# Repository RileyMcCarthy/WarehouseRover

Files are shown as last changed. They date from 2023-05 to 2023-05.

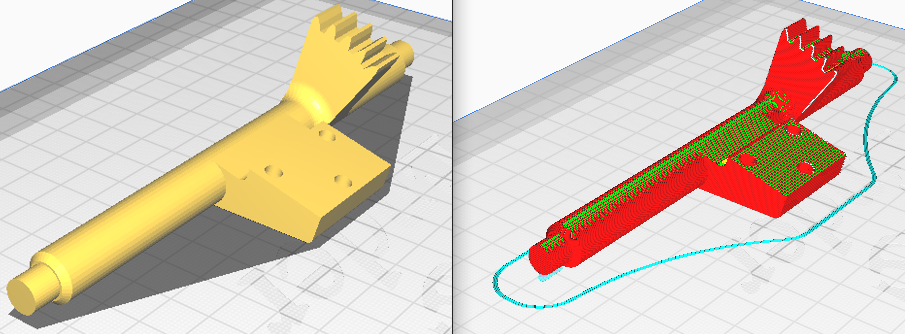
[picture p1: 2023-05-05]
Images/files/ShaftPrint.png

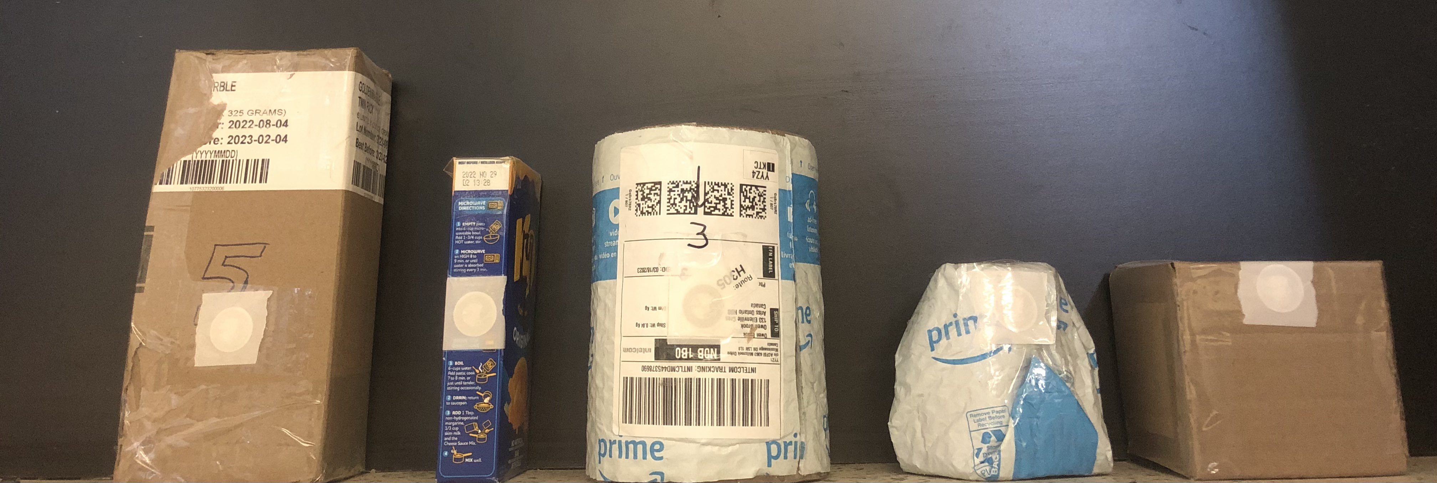
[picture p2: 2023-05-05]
Images/files/packages.jpg

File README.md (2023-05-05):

# Autonomous Sorting Mobile Robot

University of Guelph 4th year project by: Riley McCarthy, Owen Brook, Kaden Penner, Charles Peters, and Nicholas Virdiramo 

## Introduction

With the new Amazon fulfilment center being built in Cambridge, the need for automation
is ever increasing. As the number of outbound packages increase, so will the number of
returns that need to be processed. This is one example of where using automation will allow
processes to become more streamlined and efficient. Our project demonstrates the ability
of these robots in a small scale environment. We designed and developed an autonomous
sorting robot that takes packages from a starting location, identifies it, and then moves it to
the appropriate final location.

This will help the efficiency of large factories as the need for humans to move parts around
the building will be eliminated. With the new Amazon warehouse being 136,000 sqft, small
electric robots moving packages will be more efficient when compared to humans needing to
walk around.

## Objectives

The team aimed to develop an autonomous robot that sorted multiple package variations
between unique locations one at a time. The robot would receive an input from a package
at the starting location and determine the desired final location. Then autonomously would
deliver the package to the correct destination. A block diagram of the robots functions is
shown below.

**Insert block diagrm ref**

The system is completely automated, with the only external input being the placement of
the package in the starting location by a human. This mimicked the use of a conveyor belt
for accurate package delivery to the initial location. Our initial goal was to a system that
could handle three different package shapes with weight variations. This would ensure the
robot was capable of a wide verity of packages shapes and sizes, as well as a range of different
weights. Each package would have it’s own unique destination determined by an RFID sensor
to mimic a scanner being able to identify the incommoding packages and determining their
final locations.

## Mechanical Design

As the goal of the project is to both pickup and move packages, the mechanical design
needed to allow for both a movable main base, the ability to interact with the different
package sizes, and contain all the necessary parts to make the robot autonomous such as a
battery, sensors, and a micro-controller.
Shown below is the initial design of the Autonomous Sorting Mobile Robot.
While the specifics of the different components will be covered later, the motors and
ultrasonic sensors are shown, as well as the wheels, gripper mechanism, and main base of the
robot.

**Figure 2: Robot Isometric View**

The largest part of the robot is the main base. This houses the four
driving motors, two ultrasonic sensors mounts, the control system electronics, and a base for
the grippers to be fastened. Initially the base was designed to be very compact, but this
limited space under for the electronics and motors so the base was increased in size slightly
to accommodate with out overly compromising the compact design This based is designed
an manufactured to provide a strong, square foundation for the robot to operate from. The
strength of the base allowed for the robot to handle larger packages then original considered.
The square base allows for the mecanum wheels to operate as intended and no adjustment
in software needed for straight driving.

**Figure 3: Robot Base with Drive Motors, Sensors and Control System**

The gripper mechanism is driven by two motors. The first is to open and close the grippers,
while the other allows for tilting gripper assembly to lift the package off the ground. The
RFID sensor is mounted to the gripper mechanism at the base of the arms to allow for
the robot to read the package. This allows the control system to determine the correct
destination.

**Figure 4: Gripper System with RFID Sensor**

The grippers are designed to allow for the manipulation of various package sizes to be
interacted with. The initial design is shown in **Figure 4**. The design was tested and found
not to have adequate holding power for the different shapes and sizes. With the fingers of
the arms in an arc shape they only provided one point of contact and resulted in the robot
dropping packages. The arms were also found to be short not allowing enough room for the
fingers to contact he center of the package. These issues were discovered through testing,
and the solution is explained in Section 2.3.

A rack and pinion gripper design was also tested and compared to
look at the load capacity of our designs. This design is secondary and serves as a backup to
our main gripper assembly. This design may be beneficial because it is more compact and
requires less moving parts, resulting in greater grip strength. However, the rack may seize
due to friction between the rack and slide plate when the gripper is under load. For these
reasons, this gripper was not used on the final robot.

**Figure 5: Rack and Pinion Gripper**

## Fabrication

In order to physically build the robot, all the designed components were fabricated using
a 3D printer. This method was chosen as it allows for a wide range of part geometry and
features, with rapid prototyping. The group had direct access to four 3D printers, so the
fabrication of the components was not a problem. Other methods were considered but with
the accessibility and range of builds the 3D printer was chosen
Since we printed all of our parts, material selection was greatly simplified as we could
only print plastics. Furthermore, the forces involved with this robot were low enough where
material strengths did not limit the function of the robot. Plastic is also beneficial as it is
easily manipulated to fit together. Our design contains interference fits (bearings and gears)
that rely on friction and a high normal force to maintain their position. We used heat to
expanded and soften the plastic to fit the components together. Many components were also
filed and sanded after they were printed to remove imperfections from the print, such as
strings, blobs, and support material. This was especially true for parts where a precise fit
was needed or printing orientation effected quality.
Most components were printed using PLA as it is the easiest and most reliable print
material available. PETG, a more dense plastic, was also used for additional strength, for
example, the tilt shaft. The load bearing components were fabricated with 5 layers of material
on the outside surfaces for additional strength. The rest of the parts only required 2-3 layers.
Furthermore, 20-30 percent infill was used on most parts but was varied for based on the
components needs.

**Figure 6: Cura Slicer Print Estimate**

We got material estimates from Ultimaker Cura, the 3D printing slicer. This software allowed the team to understand and control the fabrication of each part.
Adjusting prints based on their geometry, fit, and function allowed for best performance. An
example of the importance of this is the fabrication of the tilt shaft. The shaft needed a
strong and circular geometry. These qualities conflict in the printing orientation, horizontal
for strength and vertical for circular geometry. This is because when it is printed horizontally
it has continuous strings of plastic along its length, increasing strength against bending.
When printed vertically the print is able to precisely outline the circular geometry and avoid
overhanging. Ultimately horizontally was chosen as the strength is more important and the
circular geometry can be adjusted by sanding after. Below shows supports under the step
in the Tilt Shaft.

**Figure 7: Cura Slicer Shaft Print Estimate**

The proposed design from report one (shown in **Figure 8**) was fabricated, assembled, and
tested. The initial testing showed that the gripper fingers were limited in their ability to pick
up the required variety of packages.

**Figure 8: Original Gripper Design**

The final gripper design was an iteration of the first design, improving on all the issues
that caused reliability problems. In the final design (shown in **Figure 9**), the arms and fingers
were redesigned to have longer reach and a pivoting crescent finger for dual point contact.
These worked flawlessly in picking up and holding the package during transportation for
several packages all with different sizes, geometry, and weight.

**Figure 9: Updated Gripper Design**

Additional mechanical testing was done to test the robot’s grip strength and ability to raise
and lower the package. Deflection of the gripper top plate was observed when the gripper
fingers closed. This is due to the torque generated by the gripper motor during package pick
up. The top plate was reinforced and reprinted to prevent failure.

## Motors and Actuators

3.1.1 Four DC Motors with Encoders
As the design places a priority on movement accuracy rather than speed, motors were
selected that contained rotary encoders, allowing for accurate tracking of the rotation of
each wheel. This allowed for a control system algorithm to be created that ensure accurate
movement. Motion planning was also incorporated ensuring adequate traction is always
maintained by limiting the acceleration of the robot’s velocity. The encoders present in these
motors contain 140 ticks per revolution. The motors were been tested to max out at 190 rpm
while running at 12v.
3.1.2 Two DC Motors with Gearboxes
In order to provide movement to the grippers, motors were used to manipulate the grippers.
To ensure the ability to manipulate packages of different sizes and weights, these motors
required sufficient torque which was provided by the gearbox. Tests were conducted to
calculate the amount of torque they were capable of providing when run at 12v. This was
determined to be 0.583 Nm of torque. These motors were controlled with the amount of
current being drawn and were programmed to hold their position when open, or a package
was sufficiently held.
3.1.3 Motor Drivers
These motors will be driven by an L293 motor driver[1]. These drivers allowed for the
motors to be speed-controlled by using pulse wave modulation (PWM). This also allowed for
the direction to be adjusted using the microcontroller.
8
GROUP 3 A.S.M. Robot
3.2 Sensors
3.2.1 Ultrasonic Sensors
To ensure accurate positioning was maintained over time, an ultrasonic sensor was used to
re-home the robot upon its return to the starting/pick-up location. This allowed the robot
to determine its current location, and adjust to ensure location error didn’t accumulate over
time. An HC-SR04 ultrasonic sensor[2] was used as it had been used by the group before,
and are easily available. It had sufficient accuracy to ensure the robot could return to the
desired location between the delivery of each package. The ultrasonic sensor has a large
range of 2cm to 400cm and an accuracy of 2mm which was adequate accuracy and range for
the purpose of our system.
3.2.2 RFID Sensor
In order to determine the final destination for each individual package, a Radio Frequency
Identification Device (RFID) was decided on. While in the future implementation, a more
widely used technology could be used. For testing, the RFID system was easy to implement,
and the component required belong to members of the group. The specific sensor used was
a MFRC522[3].
3.3 Micro-Controller
3.3.1 Arduino Mega
The microcontroller selected is the Arduino Mega, this controller was selected due to its
high amount of general-purpose input/output (GPIO) pins. Due to our limited budget, it
was also one of the few microcontrollers we had access to. Our other option, the Arduino Uno
was not selected because it would not have enough GPIO pins for all our peripherals. The
Arduino platform was convenient because it has pre-done libraries for both the Ultrasonic
sensors and the RFID sensor. It also has analog pins that were used for current sensing on
our gripper motors to determine when a package was being handled.
3.3.2 Power System
The system power was provided by a 12v LiPo battery which was connected to the motor
drivers in order to provide the required 12 volts. The voltage was also routed through a 5v
linear regulator to create the 5v needed to power the Arduino Mega, the motor driver, and
the sensors

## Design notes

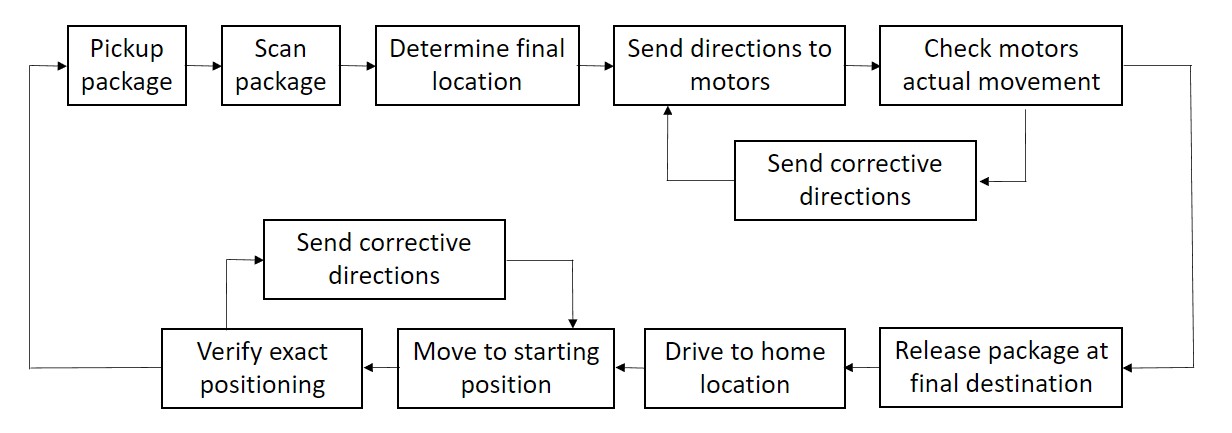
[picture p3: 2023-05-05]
Images/files/engg4480_project_proposal-block_dia.jpg

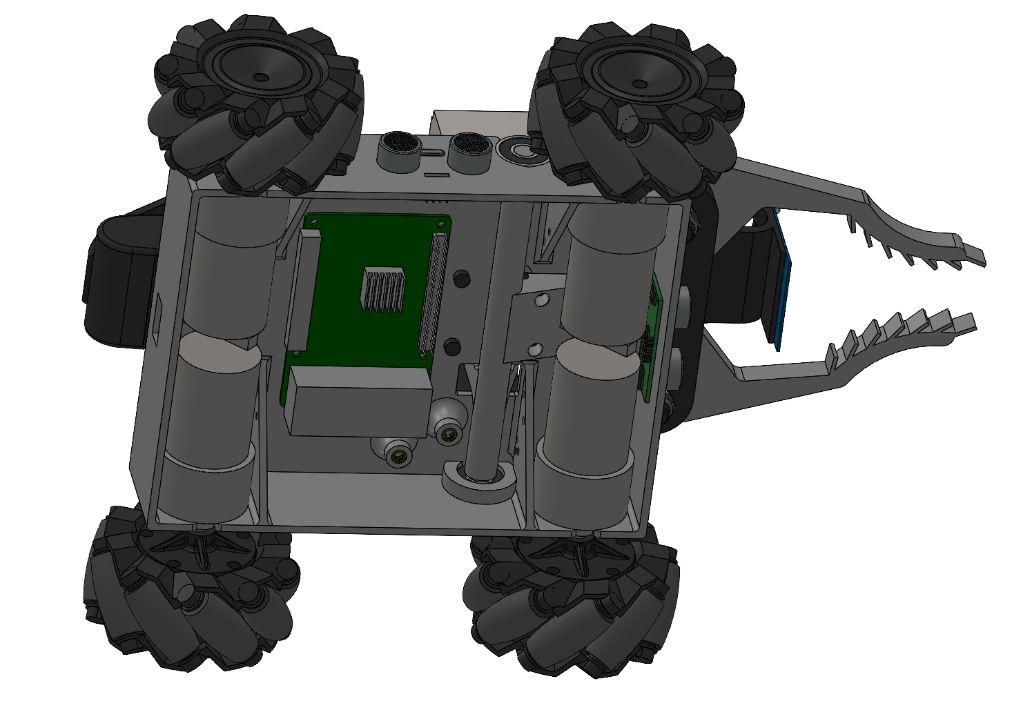
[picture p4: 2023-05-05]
Images/files/robot_btm.png

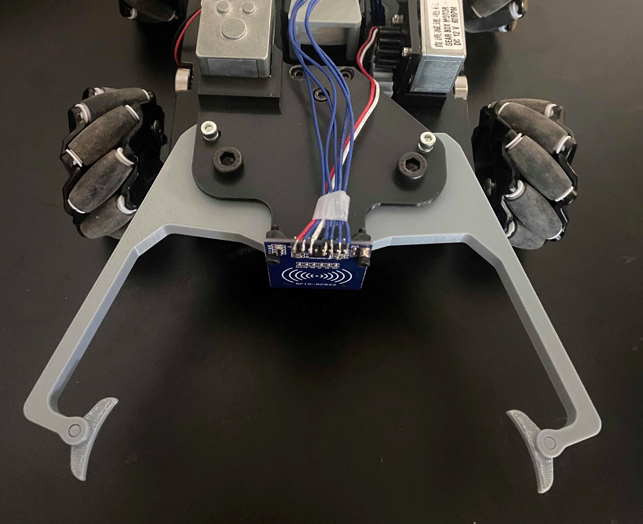
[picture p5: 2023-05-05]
Images/files/updated_gripper.jpg

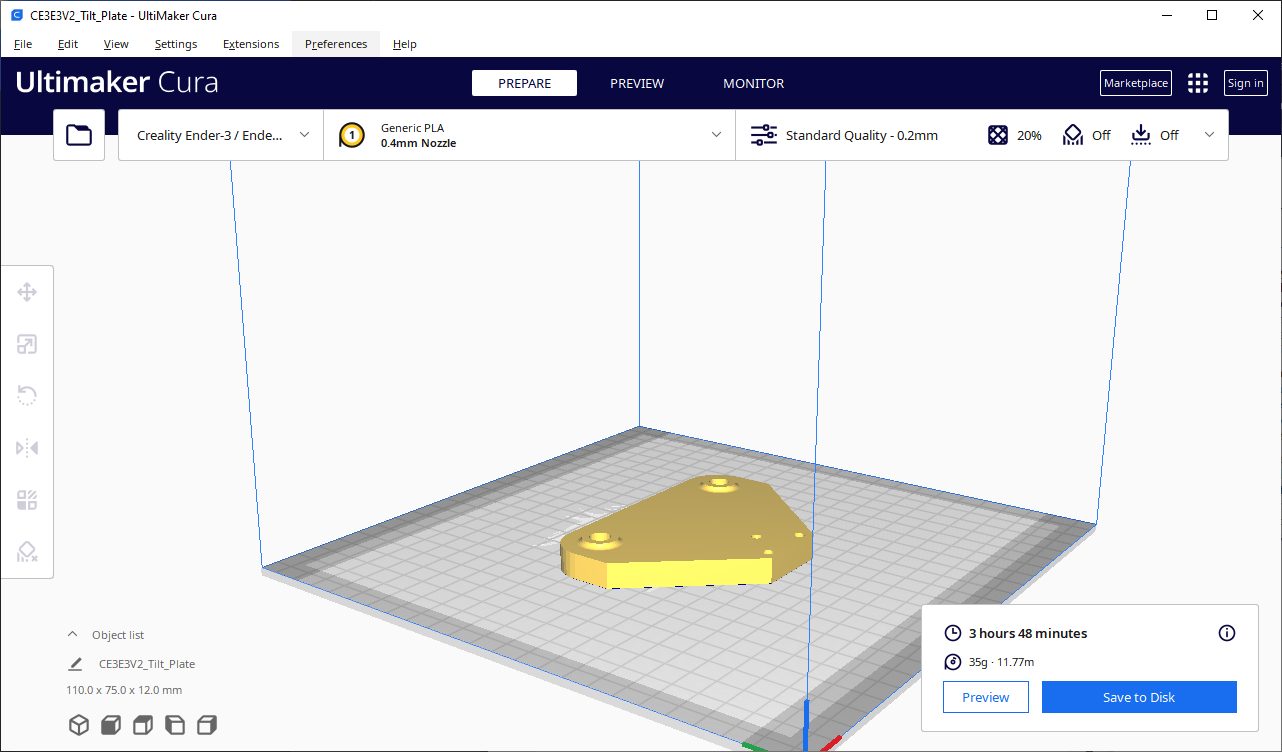
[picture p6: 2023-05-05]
Images/files/CuraSample.png

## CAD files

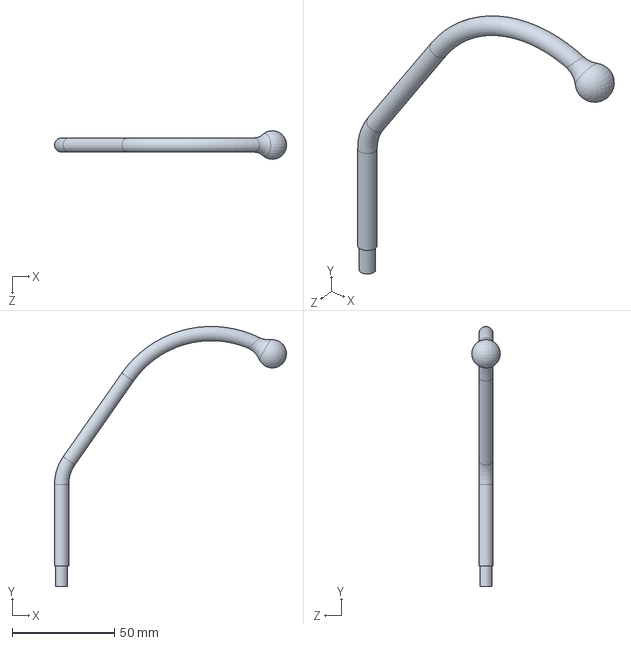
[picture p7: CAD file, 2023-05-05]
CAD/AntBody/Antenna.SLDPRT
113.6 x 127.2 x 14.0 mm

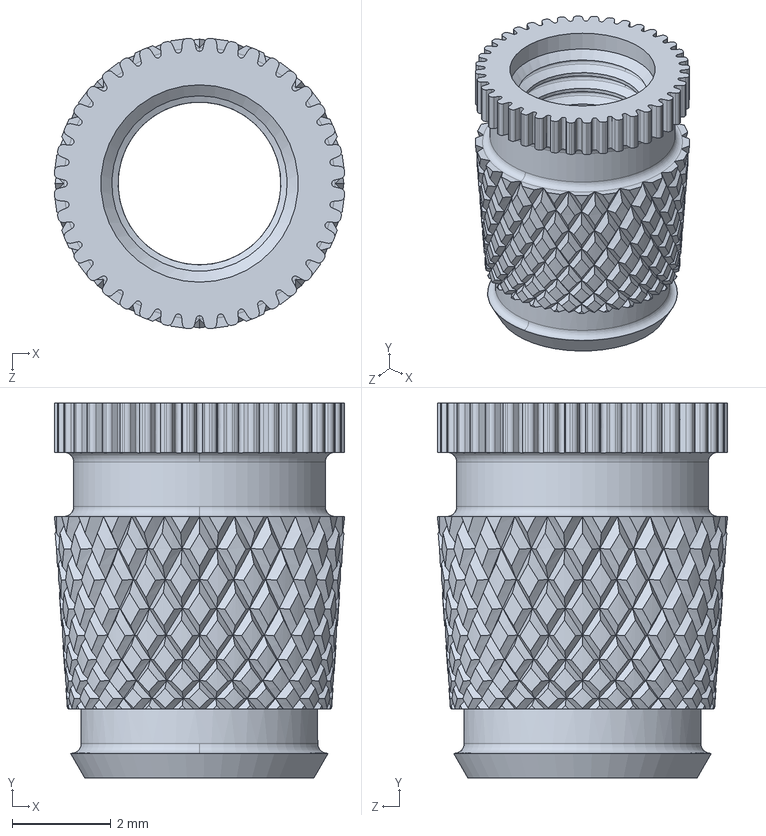
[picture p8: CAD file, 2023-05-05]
CAD/M4 threaded insert.sldprt
5.89 x 7.60 x 5.89 mm

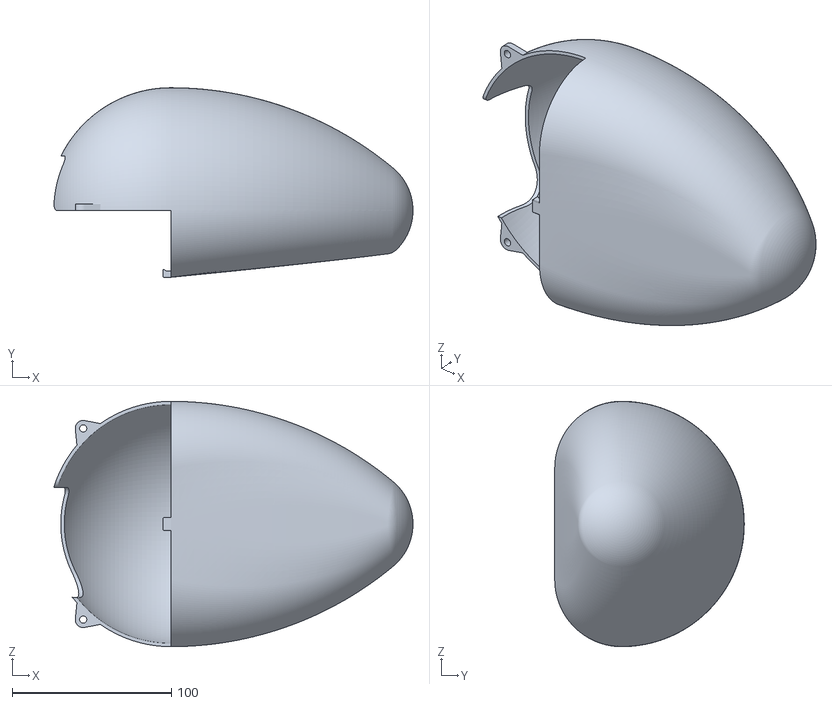
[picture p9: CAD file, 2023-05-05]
CAD/Print Files/BackBody.STL
225.3 x 119.0 x 154.0

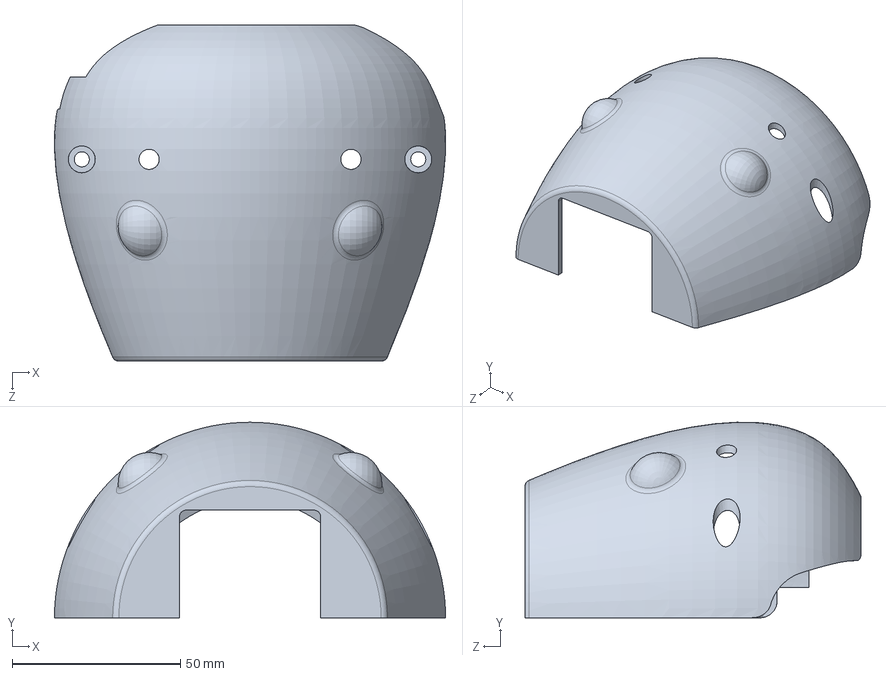
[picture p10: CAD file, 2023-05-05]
CAD/AntBody/Head.SLDPRT
116.2 x 58.1 x 100.0 mm

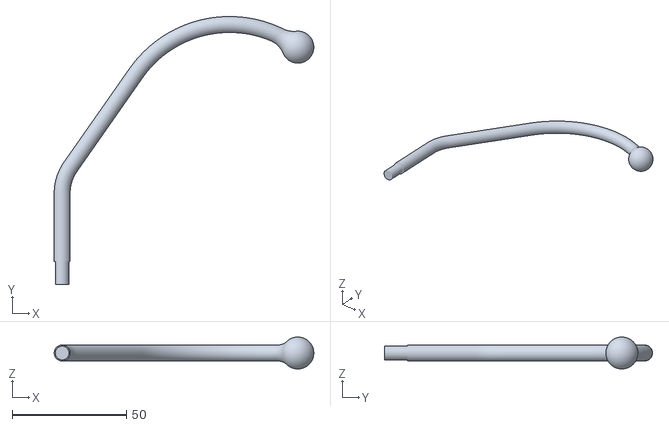
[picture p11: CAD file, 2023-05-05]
CAD/Print Files/Antenna.STL
113.6 x 117.3 x 14.0

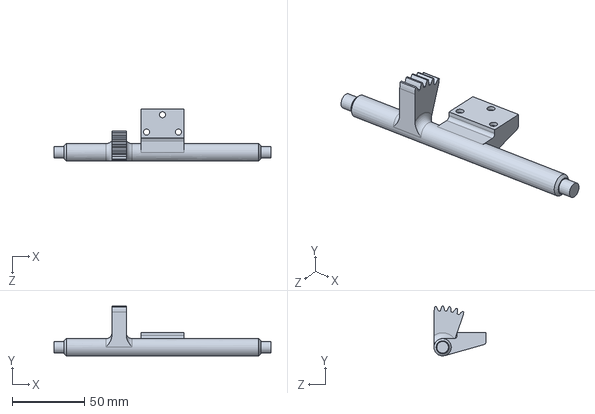
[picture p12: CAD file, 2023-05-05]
CAD/Gripper/Tilt_Shaft.SLDPRT
150.0 x 34.5 x 36.0 mm

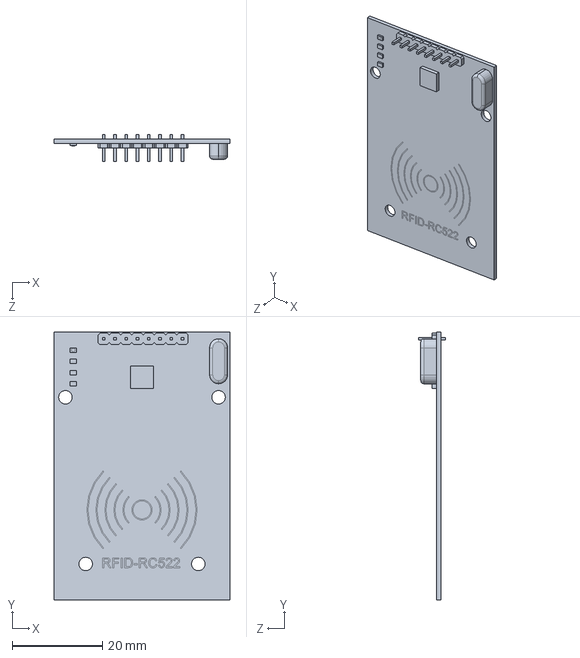
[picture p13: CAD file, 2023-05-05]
CAD/RFID-RC522 simple.SLDPRT
39.0 x 59.5 x 6.00 mm

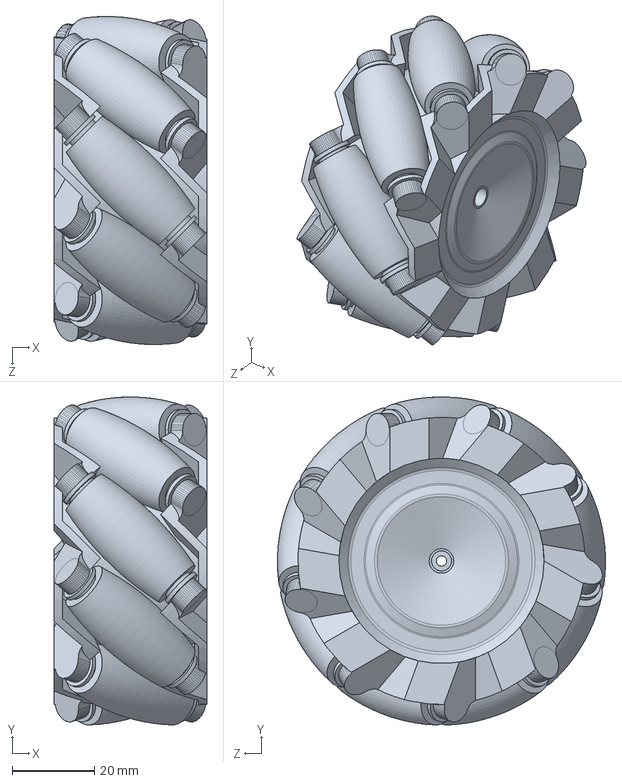
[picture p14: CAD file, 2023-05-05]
CAD/Mecanum_Wheel_RH.SLDPRT
37.2 x 80.0 x 80.0 mm

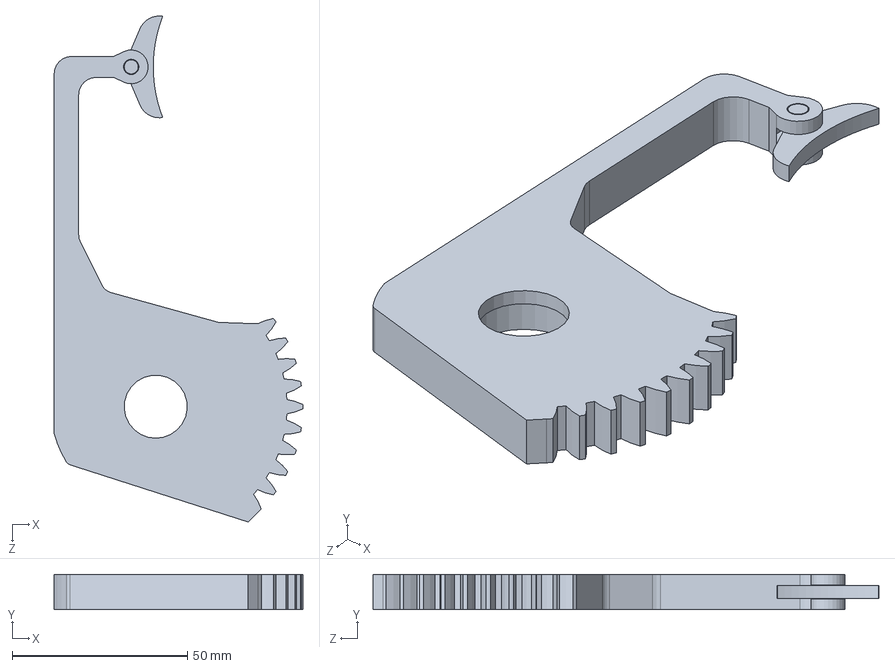
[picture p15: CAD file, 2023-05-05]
CAD/Gripper/Gripper_Finger_Slave_PrintInPlace.SLDPRT
71.0 x 10.0 x 144.5 mm

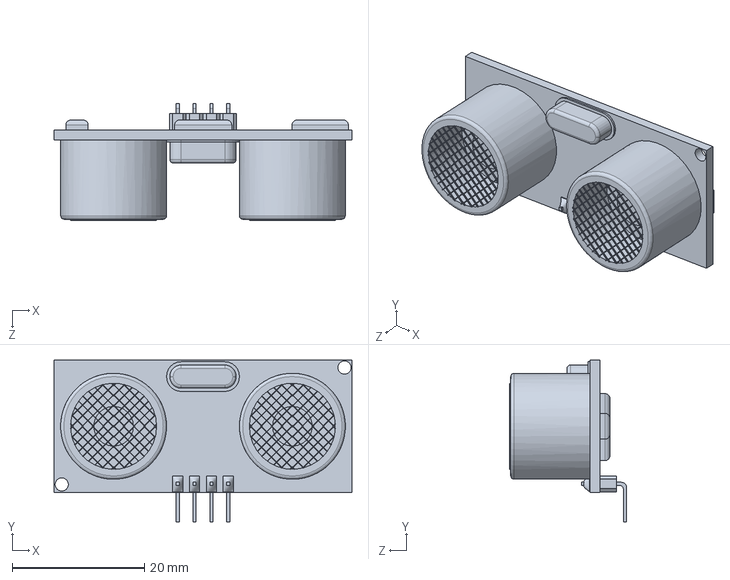
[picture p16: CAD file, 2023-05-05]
CAD/Ultrasonic_HCSR04.SLDPRT
45.0 x 24.5 x 17.7 mm

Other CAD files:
CAD/AntBody/BackBody.SLDPRT
CAD/Print Files/Head.STL
CAD/Gripper/M4x35_SHCS.SLDPRT
CAD/Gripper/M8_Nut_Nyloc.SLDPRT
CAD/Gripper/M8x40_SHCS.SLDPRT
CAD/Gripper/Old Fingers/Gripper_Finger_Master.SLDPRT
CAD/Gripper/Old Fingers/Gripper_Finger_Slave.SLDPRT
CAD/Gripper/Print Files/Gripper_Finger_Slave_PrintInPlace.STL
CAD/Gripper/Print Files/Tilt_Shaft.STL
CAD/GripperMotorMount_Vertical.SLDPRT
CAD/Hub_Pressfit.SLDPRT
CAD/LiPo_Battery.SLDPRT
CAD/M3x10.SLDPRT
CAD/M4x0.7mm Thread 18mm SHCS.SLDPRT
CAD/Print Files/Back_Plate.STL
CAD/Print Files/RobotFrame.STL
CAD/RobotFrame.SLDPRT

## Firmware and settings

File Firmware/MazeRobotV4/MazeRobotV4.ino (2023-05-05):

// Ultrasonics must use an interrupt pin each (2 total)
// Use new motion planning

//From top motors plug in with red at left side
// Motors go 1-4
#include <Arduino.h>

#include <SPI.h>
#include <MFRC522.h>

#define RST_PIN 44  // Configurable, see typical pin layout above
#define SS_PIN 49   // Configurable, see typical pin layout above

MFRC522 mfrc522(SS_PIN, RST_PIN);  // Create MFRC522 instance

#define MOTOR1_A 6
#define MOTOR1_B 24
#define ENCODER1_A 21
#define ENCODER1_B 29

#define MOTOR2_A 2
#define MOTOR2_B 26
#define ENCODER2_A 20
#define ENCODER2_B 33

#define MOTOR3_A 7
#define MOTOR3_B 40
#define ENCODER3_A 19
#define ENCODER3_B 37

#define MOTOR4_A 46
#define MOTOR4_B 48
#define ENCODER4_A 18
#define ENCODER4_B 14

#define MOTOR5_A 3
#define MOTOR5_B 34

#define MOTOR6_A 5
#define MOTOR6_B 4

#define trigPin1 47
#define echoPin1 45

#define trigPin3 45
#define echoPin3 43

#define Kp 20
#define Ki 0.01
#define Kd 0
#define T_PID_MS 0

#define MAX_ACCELERATION 300
#define MAX_VELOCITY 300

#define MOVE_ERROR 10

#define ROTATE_FACTOR 3.1

typedef struct motionPeriods_s {
  double x_goal;
  double x0;
  double v0;
  double v_max;
  double a_max;
  double T1;
  double T2;
  double T3;
  double a_acc;
  double a_dec;
  double v;
} MotionPeriod;

typedef struct setPoint_s {
  double t;
  double x;
  double v;
  double a;
} SetPoint;

typedef struct motor_s {
  bool reverse;
  int encoderA, encoderB;
  int motorA, motorB;
  long encoder;
  long encoderVelocity;
  unsigned long encoderLastTick;
  unsigned long encoderPeriod;
  long setpoint;
  long startTime;
  MotionPeriod periods;
  SetPoint motionSetpoint;
  int dir;
  long p[2], i, d;
} Motor;

typedef struct ultrasonic_s {
  int trig;
  int echo;
} Ultrasonic;

typedef enum moveType_e {
  MOVE_X,
  MOVE_Y,
  MOVE_DIAGONALLEFT,
  MOVE_DIAGONALRIGHT,
  SPIN_PLZ,
  MOVE_LIFT,  // +1 for up, -1 for down
  MOVE_GRAB,  // +1 for grab, -1 for release
} MoveType;

typedef struct Move_s {
  MoveType type;
  int delta;
  int delayms;
  bool ultrasonicCheck;
} Move;

typedef struct MoveSet_s {
  Move moves[30];
  int num_moves;
  int id;
} MoveSet;

Motor motor1;
Motor motor2;
Motor motor3;
Motor motor4;
Ultrasonic *sensor1;
Ultrasonic *sensor2;
Ultrasonic *sensor3;

#define BIN_COUNT 1

MoveSet bin_moves[BIN_COUNT];

double ultrasonic_read1(){
  pinMode(trigPin1,OUTPUT);
  digitalWrite(trigPin1, LOW);
  delayMicroseconds(5);
  digitalWrite(trigPin1, HIGH);
  delayMicroseconds(1);
  digitalWrite(trigPin1, LOW);
 
  // Read the signal from the sensor: a HIGH pulse whose
  // duration is the time (in microseconds) from the sending
  // of the ping to the reception of its echo off of an object.
  pinMode(echoPin1, INPUT);
  int duration = pulseIn(echoPin1, HIGH);
  Serial.print("readd");
  Serial.println(duration/5.8);
  return duration/5.80;
}

// Equation to determine position
double position1(double t, double xi, double vi, double a) {
  return (xi + vi * t + 0.5 * a * pow(t, 2));
}

double velocity(double t, double vi, double a) {
  return (vi + a * t);
}

void create_empty_setpoint(SetPoint *setpoint) {
  setpoint->t = 0;
  setpoint->x = 0;
  setpoint->v = 0;
  setpoint->a = 0;
}

void compute_period(MotionPeriod *periods, double x_goal, double x0, double v0, double v_max, double a_max) {
  double x_stop = fabs((-1 * v0 + sqrt(fabs(pow(v0, 2) - 4 * (-0.5 * a_max) * x0)) / (2 * (-0.5 * a_max))));

  int d;
  if (x_goal > x_stop) {
    d = 1;
  } else {
    d = -1;
  }
  int xGoalSign = 0;
  if (x_goal < 0) {
    xGoalSign = -1;
  } else if (x_goal > 0) {
    xGoalSign = 1;
  }
  int x0Sign = 0;
  if (x0 < 0) {
    x0Sign = -1;
  } else if (x0 > 0) {
    x0Sign = 1;
  }
  if (x0Sign == -1 && xGoalSign == 0) {
    d *= -1;
  }
  if (x0Sign == xGoalSign) {
    if (fabs(x0) > fabs(x_goal)) {
      Serial.println("Changing direction");
      d *= -1;
    }
  }
  double v = d * v_max;
  double a_acc = d * a_max;
  double a_dec = -1 * d * a_max;
  double T1 = fabs((v - v0) / a_acc);
  double T3 = fabs(v / a_dec);

  double X1 = position1(T1, 0, v0, a_acc);
  double X3 = position1(T3, 0, v, a_dec);

  double T2 = (x_goal - x0 - X1 - X3) / v;

  if (T2 < 0) {
    T2 = 0;
    v = d * sqrt(fabs(d * a_max * (x_goal - x0) + 0.5 * pow(v0, 2)));
    T1 = fabs((v - v0) / a_acc);
    T3 = fabs(v / a_dec);
  }
  periods->x_goal = x_goal;
  periods->x0 = x0;
  periods->v0 = v0;
  periods->v_max = v_max;
  periods->a_max = a_max;
  periods->T1 = T1;
  periods->T2 = T2;
  periods->T3 = T3;
  periods->a_acc = a_acc;
  periods->a_dec = a_dec;
  periods->v = v;
}

void compute_setpoint(SetPoint *setpoint, double t, MotionPeriod *periods) {
  double x1 = position1(periods->T1, periods->x0, periods->v0, periods->a_acc);
  double v2 = periods->v;
  double x2 = position1(periods->T2, x1, v2, 0);
  if (t <= 0) {
    setpoint->x = position1(0, periods->x0, periods->v0, 0);
    setpoint->v = velocity(0, periods->v0, 0);
    setpoint->a = 0;
  } else if (t < periods->T1) {
    setpoint->x = position1(t, periods->x0, periods->v0, periods->a_acc);
    setpoint->v = velocity(t, periods->v0, periods->a_acc);
    setpoint->a = periods->a_acc;
  } else if (t < periods->T1 + periods->T2) {
    setpoint->x = position1(t - periods->T1, x1, v2, 0);
    setpoint->v = velocity(t - periods->T1, v2, 0);
    setpoint->a = 0;
  } else if (t < periods->T1 + periods->T2 + periods->T3) {
    setpoint->x = position1(t - (periods->T1 + periods->T2), x2, v2, periods->a_dec);
    setpoint->v = velocity(t - (periods->T1 + periods->T2), v2, periods->a_dec);
    setpoint->a = periods->a_dec;
  } else {
    setpoint->x = periods->x_goal;
    setpoint->v = 0;
    setpoint->a = 0;
  }
}

double mm_to_ticks(int mm) {
  //140ticks/rev / 80mm/rev * mm
  return mm * (140.0 / (3.14159 * 80.0));
}

double ticks_to_mm(int ticks) {
  return ((double)ticks) / (140.0 / (3.14159 * 80.0));
}

void inc_a1() {
  int increment = 1;
  if (!motor1.reverse) {
    increment = -1;
  }
  if (digitalRead(motor1.encoderB)) {  //B->A
    motor1.encoder -= increment;
  } else {
    motor1.encoder += increment;
  }
}

void inc_a2() {
  int increment = 1;
  if (!motor2.reverse) {
    increment = -1;
  }
  if (digitalRead(motor2.encoderB)) {  //B->A
    motor2.encoder -= increment;
  } else {
    motor2.encoder += increment;
  }
}

void inc_a3() {
  int increment = 1;
  if (motor3.reverse) {
    increment = -1;
  }
  if (digitalRead(motor3.encoderB)) {  //B->A
    motor3.encoder -= increment;
  } else {
    motor3.encoder += increment;
  }
}

void inc_a4() {
  int increment = 1;
  if (motor4.reverse) {
    increment = -1;
  }
  if (digitalRead(motor4.encoderB)) {  //B->A
    motor4.encoder -= increment;
  } else {
    motor4.encoder += increment;
  }
}

void setup_motor(Motor *motor, int motorA, int motorB, int encoderA, int encoderB, bool reverse, int id, void (*func)()) {
  motor->encoder = 0;
  motor->encoderLastTick = 0;
  motor->encoderPeriod = 0;
  motor->startTime = 0;
  motor->setpoint = 0;
  motor->reverse = reverse;
  motor->p[0] = 0;
  motor->p[1] = 0;
  motor->i = 0;
  motor->d = 0;
  motor->motorA = motorA;
  motor->motorB = motorB;
  motor->encoderA = encoderA;
  motor->encoderB = encoderB;
  motor->periods.x_goal = 0;
  motor->periods.x0 = 0;
  motor->periods.v0 = 0;
  motor->periods.v_max = 0;
  motor->periods.a_max = 0;
  motor->periods.T1 = 0;
  motor->periods.T2 = 0;
  motor->periods.T3 = 0;
  motor->periods.a_acc = 0;
  motor->periods.a_dec = 0;
  motor->periods.v = 0;
  motor->motionSetpoint.t = 0;
  motor->motionSetpoint.x = 0;
  motor->motionSetpoint.v = 0;
  motor->motionSetpoint.a = 0;
  motor->dir = 0;
  pinMode(motor->encoderA, INPUT);
  pinMode(motor->encoderB, INPUT);
  pinMode(motor->motorA, OUTPUT);
  pinMode(motor->motorB, OUTPUT);
  attachInterrupt(digitalPinToInterrupt(motor->encoderA), func, RISING);
}

void move_relative(Motor *motor, int setpoint) {
  double currentmm = ticks_to_mm(motor->encoder);
  motor->setpoint += setpoint;
  compute_period(&(motor->periods), motor->setpoint, currentmm, 0, MAX_VELOCITY, MAX_ACCELERATION);
  /*  Serial.print("Currentmm:");
  Serial.println(currentmm);
  Serial.print("t1:");
  Serial.println(motor->periods.T1);
  Serial.print("t2:");
  Serial.println(motor->periods.T2);
  Serial.print("t3:");
  Serial.println(motor->periods.T3);
  Serial.print("Currentmm:");
  Serial.println(motor->periods.T3);*/
  motor->startTime = millis();
}


void motor_pid_update(Motor *motor) {
  //PID Variables
  long currentTime = millis();
  long deltaTime = currentTime - motor->startTime;
  double velocity = 0;
  compute_setpoint(&(motor->motionSetpoint), deltaTime / 1000.0, &(motor->periods));
  int limitedSetpoint = (int)mm_to_ticks(motor->motionSetpoint.x);


  //Update PID values
  motor->p[1] = motor->p[0];
  motor->p[0] = limitedSetpoint - motor->encoder;
  motor->i += motor->p[0];
  motor->d = (motor->p[0] - motor->p[1]);

  //Update motor voltage from setpoint
  int voltage = motor->p[0] * Kp + motor->i * Ki + motor->d * Kd;
  if (motor->reverse) {
    voltage = voltage * -1;
  }

  int v_abs = fabs(voltage);
  if (v_abs > 255)
    v_abs = 255;
  if (voltage > 0) {  //Move CW
    analogWrite(motor->motorA, 255 - v_abs);
    digitalWrite(motor->motorB, HIGH);
  } else {  //Move CCW
    digitalWrite(motor->motorB, LOW);
    analogWrite(motor->motorA, v_abs);
  }
}


long nextMove;

void setup() {

  Serial.begin(9600);

  SPI.begin();                        // Init SPI bus
  mfrc522.PCD_Init();                 // Init MFRC522
  delay(4);                           // Optional delay. Some board do need more time after init to be ready, see Readme
  mfrc522.PCD_DumpVersionToSerial();  // Show details of PCD - MFRC522 Card Reader details
  Serial.println(F("Scan PICC to see UID, SAK, type, and data blocks..."));
  delay(1000);

  nextMove = 0;

  setup_motor(&motor1, MOTOR1_A, MOTOR1_B, ENCODER1_A, ENCODER1_B, false, 1, inc_a1);
  setup_motor(&motor2, MOTOR2_A, MOTOR2_B, ENCODER2_A, ENCODER2_B, true, 2, inc_a2);
  setup_motor(&motor3, MOTOR3_A, MOTOR3_B, ENCODER3_A, ENCODER3_B, false, 3, inc_a3);
  setup_motor(&motor4, MOTOR4_A, MOTOR4_B, ENCODER4_A, ENCODER4_B, true, 4, inc_a4);

  //pinMode(trigPin1,OUTPUT);
  //pinMode(echoPin1,INPUT);

  bin_moves[0].id = 62;  // Box #4

  //STANDARD MOVE START
  bin_moves[0].moves[0].type = MOVE_GRAB;
  bin_moves[0].moves[0].delta = 1;
  bin_moves[0].moves[0].delayms = 500;
  bin_moves[0].moves[0].ultrasonicCheck = false;

  bin_moves[0].moves[1].type = MOVE_LIFT;
  bin_moves[0].moves[1].delta = 1;
  bin_moves[0].moves[1].delayms = 300;
  bin_moves[0].moves[1].ultrasonicCheck = false;

  bin_moves[0].moves[2].type = MOVE_X;
  bin_moves[0].moves[2].delta = -914;
  bin_moves[0].moves[2].delayms = 5000;
  bin_moves[0].moves[2].ultrasonicCheck = false;

  bin_moves[0].moves[3].type = SPIN_PLZ;
  bin_moves[0].moves[3].delta = -90;
  bin_moves[0].moves[3].delayms = 5000;
  bin_moves[0].moves[3].ultrasonicCheck = false;

  bin_moves[0].moves[4].type = MOVE_X;
  bin_moves[0].moves[4].delta = 3048;
  bin_moves[0].moves[4].delayms = 5000;
  bin_moves[0].moves[4].ultrasonicCheck = false;
  //STANDARD MOVE END

  bin_moves[0].moves[5].type = MOVE_Y;
  bin_moves[0].moves[5].delta = -394;
  bin_moves[0].moves[5].delayms = 5000;
  bin_moves[0].moves[5].ultrasonicCheck = false;

  //STANDARD MOVE START
  bin_moves[0].moves[6].type = MOVE_X;
  bin_moves[0].moves[6].delta = 600;
  bin_moves[0].moves[6].delayms = 5000;
  bin_moves[0].moves[6].ultrasonicCheck = false;

  bin_moves[0].moves[7].type = MOVE_LIFT;
  bin_moves[0].moves[7].delta = -1;
  bin_moves[0].moves[7].delayms = 300;
  bin_moves[0].moves[7].ultrasonicCheck = false;

  bin_moves[0].moves[8].type = MOVE_GRAB;
  bin_moves[0].moves[8].delta = -1;
  bin_moves[0].moves[8].delayms = 500;
  bin_moves[0].moves[8].ultrasonicCheck = false;

  bin_moves[0].moves[9].type = MOVE_LIFT;
  bin_moves[0].moves[9].delta = -1;
  bin_moves[0].moves[9].delayms = 100;
  bin_moves[0].moves[9].ultrasonicCheck = false;

  bin_moves[0].moves[10].type = MOVE_X;
  bin_moves[0].moves[10].delta = -600;
  bin_moves[0].moves[10].delayms = 5000;
  bin_moves[0].moves[10].ultrasonicCheck = false;
  //STANDARD MOVE END

  bin_moves[0].moves[11].type = MOVE_Y;
  bin_moves[0].moves[11].delta = 394;
  bin_moves[0].moves[11].delayms = 5000;
  bin_moves[0].moves[11].ultrasonicCheck = false;

  //STANDARD MOVE START
  bin_moves[0].moves[12].type = SPIN_PLZ;
  bin_moves[0].moves[12].delta = -180;
  bin_moves[0].moves[12].delayms = 5000;
  bin_moves[0].moves[12].ultrasonicCheck = false;

  bin_moves[0].moves[13].type = MOVE_X;
  bin_moves[0].moves[13].delta = 3048;
  bin_moves[0].moves[13].delayms = 5000;
  bin_moves[0].moves[13].ultrasonicCheck = false;

  bin_moves[0].moves[14].type = SPIN_PLZ;
  bin_moves[0].moves[14].delta = 90;
  bin_moves[0].moves[14].delayms = 5000;
  bin_moves[0].moves[14].ultrasonicCheck = false;

  bin_moves[0].moves[15].type = MOVE_X;
  bin_moves[0].moves[15].delta = 914;
  bin_moves[0].moves[15].delayms = 5000;
  bin_moves[0].moves[15].ultrasonicCheck = false;
  int index = 16;
  bin_moves[0].moves[index].type = MOVE_Y;
  bin_moves[0].moves[index].delta = 250;
  bin_moves[0].moves[index].delayms = 300;
  bin_moves[0].moves[index].ultrasonicCheck = false;
  index++;

  bin_moves[0].moves[index].type = MOVE_Y;
  bin_moves[0].moves[index].delta = -190;
  bin_moves[0].moves[index].delayms = 300;
  bin_moves[0].moves[index].ultrasonicCheck = false;
  index++;

  bin_moves[0].moves[index].type = MOVE_X;
  bin_moves[0].moves[index].delta = 250;
  bin_moves[0].moves[index].delayms = 300;
  bin_moves[0].moves[index].ultrasonicCheck = true;
  index++;
  bin_moves[0].num_moves = index;
  //MOVE END, SHOULD WAIT FOR RFID READ FOR NEXT MOVESET


  //new package
  /*memcpy(&(bin_moves[1]),bin_moves[0],sizeof(bin_moves[0]));
  bin_moves[1].id = 63;
  bin_moves[1].moves[5].delta = -394; //new movement
  bin_moves[1].moves[11].delta = 394; //new movement*/

}

typedef enum stages_e {
  HOME,
  PACKAGE_WAIT,
  GRAB_PACKAGE,
  RFID_READ,
  MOVE_TO_BIN
} Stages;

void execute_move(Move *move) {

  switch (move->type) {
    case MOVE_X:
      if (move->ultrasonicCheck)
      {
        double distance = ultrasonic_read1();
        double difference = distance-move->delta;
        Serial.print("diff");
        Serial.println(difference);
        move_relative(&motor1, difference);
        move_relative(&motor2, difference);
        move_relative(&motor3, difference);
        move_relative(&motor4, difference);
        break;
      }
      move_relative(&motor1, move->delta);
      move_relative(&motor2, move->delta);
      move_relative(&motor3, move->delta);
      move_relative(&motor4, move->delta);
      break;
    case MOVE_Y:
      move_relative(&motor1, -1 * move->delta);
      move_relative(&motor2, move->delta);
      move_relative(&motor3, -1 * move->delta);
      move_relative(&motor4, move->delta);
      break;
    case MOVE_DIAGONALRIGHT:
      move_relative(&motor1, move->delta);
      move_relative(&motor2, 1);
      move_relative(&motor3, move->delta);
      move_relative(&motor4, 1);
      break;
    case MOVE_DIAGONALLEFT:
      move_relative(&motor1, 1);
      move_relative(&motor2, move->delta);
      move_relative(&motor3, 1);
      move_relative(&motor4, move->delta);
      break;
    case SPIN_PLZ:
      move_relative(&motor1, -1 * move->delta * ROTATE_FACTOR);
      move_relative(&motor2, move->delta * ROTATE_FACTOR);
      move_relative(&motor3, move->delta * ROTATE_FACTOR);
      move_relative(&motor4, -1 * move->delta * ROTATE_FACTOR);
      break;
    case MOVE_LIFT:
      if (move->delta > 0) {
        analogWrite(MOTOR6_A, 255);
        digitalWrite(MOTOR6_B, LOW);
        delay(move->delayms);
        analogWrite(MOTOR6_A, 0);
        digitalWrite(MOTOR6_B, 0);
      } else {
        analogWrite(MOTOR6_A, 0);
        digitalWrite(MOTOR6_B, HIGH);
        delay(move->delayms);
        analogWrite(MOTOR6_A, 0);
        digitalWrite(MOTOR6_B, 0);
      }
      delay(1000);
      break;
    case MOVE_GRAB:

      if (move->delta > 0) {
        analogWrite(MOTOR5_A, 255);
        digitalWrite(MOTOR5_B, LOW);
        delay(move->delayms);
        analogWrite(MOTOR5_A, 0);
        digitalWrite(MOTOR5_B, 0);
      } else {
        analogWrite(MOTOR5_A, 0);
        digitalWrite(MOTOR5_B, HIGH);
        delay(move->delayms);
        analogWrite(MOTOR5_A, 0);
        digitalWrite(MOTOR5_B, 0);
      }
      delay(1000);
      break;
  }
}

MoveSet *find_moveset_by_id(int id) {
  for (int i = 0; i < BIN_COUNT; i++) {
    if (bin_moves[i].id == id) {
      Serial.print("Found moveset with id:");
      Serial.println(bin_moves[i].id);
      return &(bin_moves[i]);
    }
  }
  return NULL;  // no moveset found
}
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
void loop() {

  // Move can be X,Y,DiAG_LEFT,DIAG_RIGHT,ROTATE
  // X,Y can be ultrasonic moves that determine distance sensors should read for position
  // MoveSet is a sequence of moves that should be executed

  // Cycle through stages
  // Start
  // Stage 0 -> Home robot (read ultrasonic sensors for reference, then move by offset to home position)
  // Stage 1 ->  wait for package (read ultrasonic sensor)
  // Package detected
  // Stage 2 -> move forward, pick up package, move backwards to home
  // Stage 3 -> Read package RFID sensor id
  // IF FAILURE: id cannot be read, return package and wait for package adjustment (Undo last moveset return to start)
  // Stage 4 -> Execute move set for package id (moves to bin, place package, undo moveset)
  // Return to start
  //double distance = ultrasonic_read1();
  //Serial.println(distance);
  //delay(1000);
  //return;
  int stage = HOME;
  long next_pid_update_ms = 0;

  int moveSetIndex = 0;
  bool new_move = false;

  MoveSet *currentMoveSet = NULL;
  MoveSet startingMoveSet;
  int index = 0;
  //open grippers, tilt down
  startingMoveSet.moves[index].type = MOVE_LIFT;
  startingMoveSet.moves[index].delta = -1;
  startingMoveSet.moves[index].delayms = 500;
  startingMoveSet.moves[index].ultrasonicCheck = false;
  index++;

  startingMoveSet.moves[index].type = MOVE_GRAB;
  startingMoveSet.moves[index].delta = 1;
  startingMoveSet.moves[index].delayms = 300;
  startingMoveSet.moves[index].ultrasonicCheck = false;
  index++;

  startingMoveSet.moves[index].type = MOVE_Y;
  startingMoveSet.moves[index].delta = 250;
  startingMoveSet.moves[index].delayms = 300;
  startingMoveSet.moves[index].ultrasonicCheck = false;
  index++;

  startingMoveSet.moves[index].type = MOVE_Y;
  startingMoveSet.moves[index].delta = -190;
  startingMoveSet.moves[index].delayms = 300;
  startingMoveSet.moves[index].ultrasonicCheck = false;
  index++;

  startingMoveSet.moves[index].type = MOVE_X;
  startingMoveSet.moves[index].delta = 250;
  startingMoveSet.moves[index].delayms = 300;
  startingMoveSet.moves[index].ultrasonicCheck = true;
  index++;

  startingMoveSet.moves[index].type = MOVE_GRAB;
  startingMoveSet.moves[index].delta = -1;
  startingMoveSet.moves[index].delayms = 300;
  startingMoveSet.moves[index].ultrasonicCheck = false;
  index++;

  /*startingMoveSet.moves[index].type = MOVE_DIAGONALLEFT;
  startingMoveSet.moves[index].delta = -300;
  startingMoveSet.moves[index].delayms = 300;
  startingMoveSet.moves[index].ultrasonicCheck = false;
  index++;*/
  startingMoveSet.num_moves = index;
  //waiting for rfid

  currentMoveSet = &startingMoveSet;
  int lastMoveIndex = -1;
  int lastCompletedMove = -1;
  while (true) {
    //update motor PID
    if (millis() > next_pid_update_ms) {
      //Serial.println("Updating PID");
      motor_pid_update(&motor1);
      motor_pid_update(&motor2);
      motor_pid_update(&motor3);
      motor_pid_update(&motor4);
      next_pid_update_ms = millis() + T_PID_MS;
    }
    if (millis() < nextMove) {
      continue;
    }
    if (currentMoveSet == NULL) {

      //Serial.println("Waiting for RFID");
      // wait for rfid to get next move set
      // Reset the loop if no new card present on the sensor/reader. This saves the entire process when idle.
      if 
      currentpackage++;
      currentMoveSet = find_moveset_by_id(currentpackage);
      moveSetIndex = 0;
      lastMoveIndex = -1;
    }

    if ((currentMoveSet != NULL) && (lastMoveIndex != moveSetIndex)) {
      Serial.print("Move started: ");
      Serial.println(moveSetIndex);
      execute_move(&(currentMoveSet->moves[moveSetIndex]));
      lastMoveIndex = moveSetIndex;
    }

    int motor1AbsError = fabs(motor1.setpoint - ticks_to_mm(motor1.encoder));
    int motor2AbsError = fabs(motor2.setpoint - ticks_to_mm(motor2.encoder));
    int motor3AbsError = fabs(motor3.setpoint - ticks_to_mm(motor3.encoder));
    int motor4AbsError = fabs(motor4.setpoint - ticks_to_mm(motor4.encoder));
    //Serial.println(motor1AbsError);
    if (motor1AbsError < MOVE_ERROR && motor2AbsError < MOVE_ERROR && motor3AbsError < MOVE_ERROR && motor4AbsError < MOVE_ERROR && currentMoveSet != NULL) {
      // Move complete
      Serial.println("Move complete");
      nextMove = millis() + 1000;
      moveSetIndex++;
      if (moveSetIndex >= currentMoveSet->num_moves) {
        Serial.println("MoveSet complete");
        moveSetIndex = 0;
        lastMoveIndex = -1;
        currentMoveSet = NULL;
      }
    }
  }

  //delay(10);
}
